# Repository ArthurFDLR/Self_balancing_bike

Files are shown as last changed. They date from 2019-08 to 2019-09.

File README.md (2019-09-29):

# Self_balancing_bike

The final objective is to stabilize a bike using a flywheel. For now, I'm focusing on the stabilisation part : reading IMU data, precise DC motor control, PID controller ...

## Mecanical parts
### Frame 
I wanted something as simple as possible. I initialy printed a single arm supported wheel. However the mass of the wheel was way to much for the frame to handle. I added a second arm to hold the wheel thanks to a bearing. The height of the rotationnal axis is variable. Once in place, toothpicks lock the position.

### Flywheel
Theorically I could determine the momentum of the wheel. However the equation depends on way to many factors to be really usable from the ground up. I've simply use an aluminum wheel I had laying around. I'll eventually change it to achieve a better efficiency.

## Electronics

Nothing to fancy here. A simple Nano v3 to compute the data, a MD13S motor driver with a Pololu 6V 25mm motor and an MPU6050. I'll certainly swap those componnent for a single board like a Storm32-BGC V1.32 usually used for gimbals. It has all I need (and even more) for this project.

## Code

The main goal is to get an efficiente code that can run as fast as possible on the Nano. For exemple I access directly to Atmega's registers during ISR. Currently runing at ~60Hz.
To ease tunings, a serial communication between the board and the IDE is setup to tune certain values and choose mode in real-time. 

| Char command | Mode |
| - | --- |
| 1 | Running stabilisation |
| 2 | Motor test w/ potentiometer |
| 3 | Setpoint variation viewer |
| 4 | IMU data viewer |
| p | KP tuning |
| i | KI tuning |
| d | KD tuning |
| s | KS tuning |

I use the incredible [library i2cdevlib from jrowberg](https://github.com/jrowberg/i2cdevlib) which takes advantage of the internal DMP of the board to read the IMU.

```c++
// IN   // NULL
// OUT  // ypr : float[3]
// DO   // Read last available data from MPU6050. Update {Yaw,Pitch,Roll} angular position in ypr
void Update_leanAngle();

// IN   // ypr                           : float[3]
        // IMU_time_now, IMU_time_prev   : uint32_t
// OUT  // leanAngle                     : float
        // leanAngle_smoothed            : float
        // leanAngleError                : float
        // leanAngle_Integer             : float
        // leanAngle_derivative          : float
        // leanAngle_derivative_smoothed : float
        // leanAngleSetPoint             : float
// TUNE // leanAngle_Filter              : float
        // leanAngle_Derivative_Filter   : float
        // leanAngle_HeavyFilter         : float
        // setPoint_KP, setPoint_KD      : uint32_t
// DO   // Calculates lean angle and its derivative and integral from ypr.
        // Filter results to eliminate noise (exponential filter)
void leanAngle_compute();

// IN   // motorCommandPwm : int16_t
        // motorSpeedRpm   : uint32_t
// OUT  // NULL
// TUNE // motorCommandPwm_Offset         : int16_t
        // motorCommandPwm_Starter_Offset : int16_t
        // motorLimitPwm                  : int16_t
// DO   // Filters command and send to motor. Smooth start, offset, limit ...
void Set_Motor_Speed();

// IN   // motorTickCount    : int32_t
// OUT  // motorSpeedRpm     : uint32_t
        // motorDirection    : int8_t
        // motorAccelerating : bool
// TUNE // motorFilter : float
// DO   // Interpret encoder ticks to give motor speed
void Update_MotorData();

// IN   // leanAngleError       : float
        // leanAngle_Integer    : float
        // leanAngle_derivative : float
        // motorDirection       : int8_t
        // motorSpeedRpm        : uint32_t
// OUT  // PID_output           : double
// TUNE // KP, KI, KD, KS       : float
        // motorFriction        : uint32_t
        // motorLimitPwm        : int16_t
// DO   // Compute data to give command w/PID controller
void Update_MotorData();
```

## Current state

IMU data viewer (http://www.youtube.com/watch?v=QBGMhSDM0Ms "IMU data viewer")

I didn't find any way to start the motor without it giving a strong hit. It leads to an overshooting when trying to stabilize when the motor is still, for any KP ... I tried to set the standard rotation speed around PWM=40. I achieved some good reaction but only one falling side at a time. The braking power of the motor is way stronger than it's acceleration. It would recquiere an adaptive PID tuning given wheel rotation acceleration sign. Even then, it would be higly unefficient.
I'm now trying to fit a gimbal brushless motor - 120kv -. With a descent control method, I'll eventually overcome the jerkyness at low speed.

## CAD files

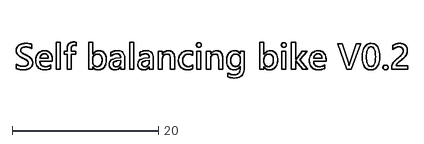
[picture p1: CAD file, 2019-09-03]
3D_Models/Catia_project/txt_mark.dxf
53.5 x 4.93

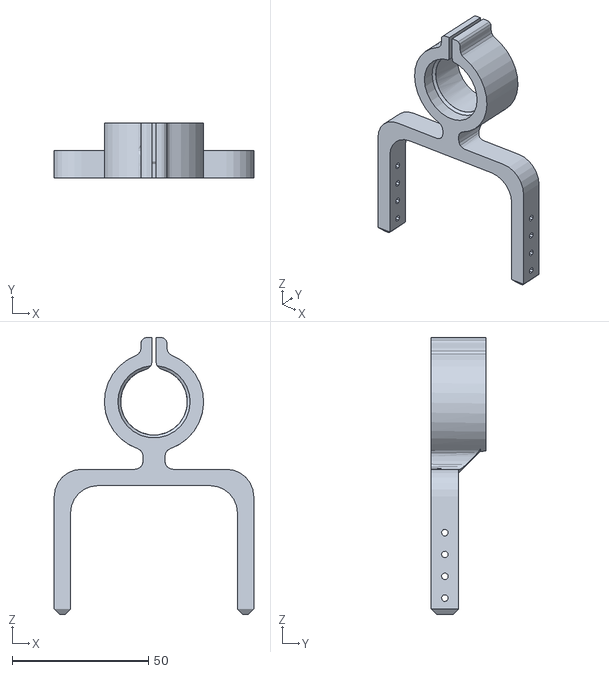
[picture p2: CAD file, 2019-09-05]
3D_Models/Motor_holder.stl
73.2 x 20.0 x 101.6

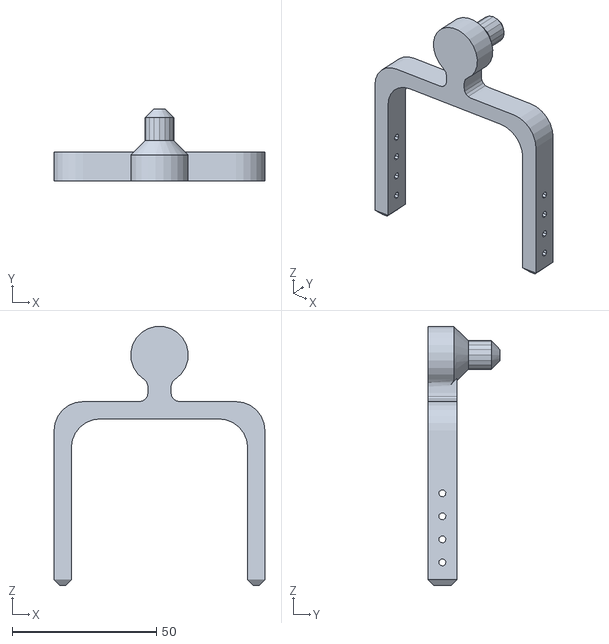
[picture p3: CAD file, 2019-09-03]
3D_Models/Wheel_holder.stl
73.2 x 25.0 x 89.9

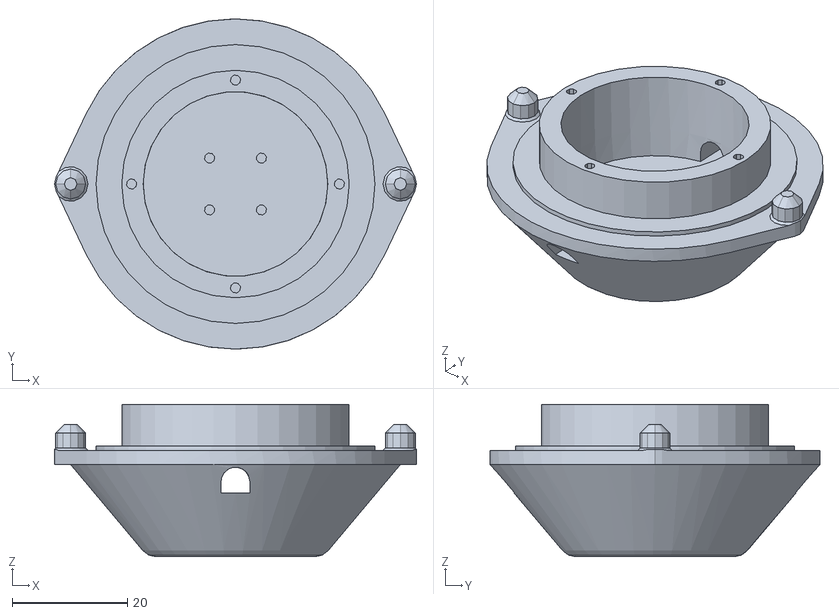
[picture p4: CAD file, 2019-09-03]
3D_Models/InertiaWheel_mount_front_V3.stl
62.7 x 57.2 x 26.4

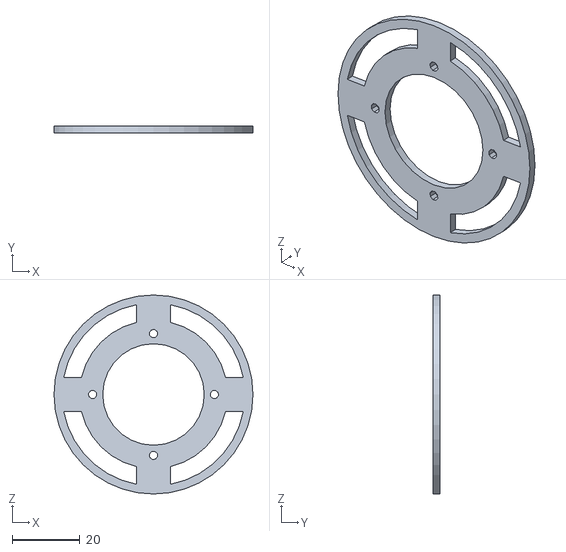
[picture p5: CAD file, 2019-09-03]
3D_Models/InertiaWheel_mount_back.stl
58.8 x 2.00 x 58.8

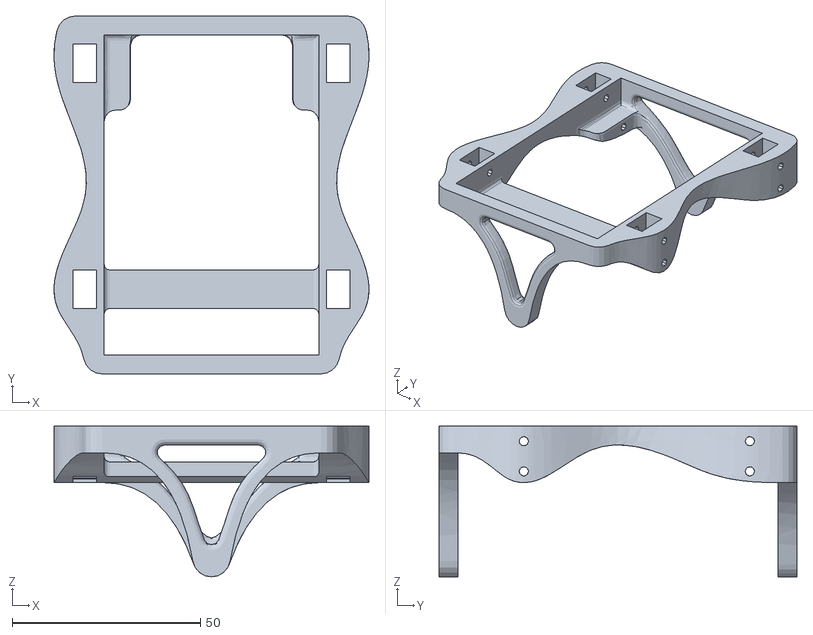
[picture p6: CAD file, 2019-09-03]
3D_Models/Lower_part_balancing.stl
83.6 x 95.0 x 40.0

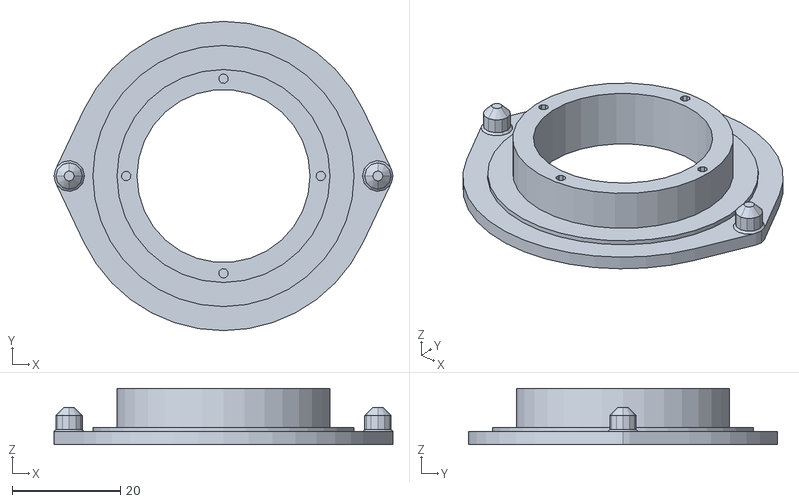
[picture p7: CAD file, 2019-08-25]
3D_Models/InertiaWheel_mount_V1.stl
62.7 x 57.2 x 10.4

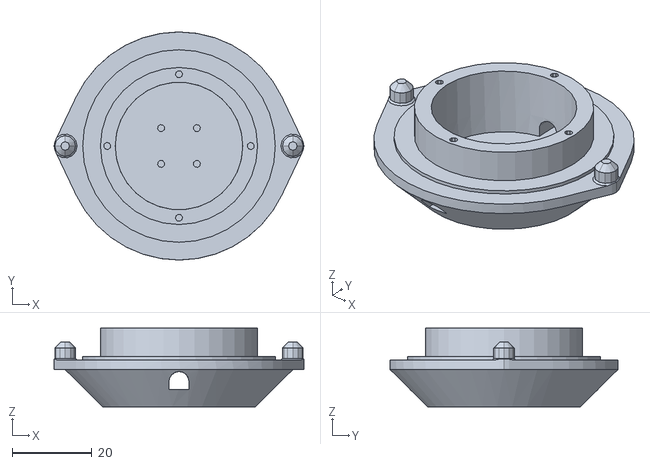
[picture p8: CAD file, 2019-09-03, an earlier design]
3D_Models/InertiaWheel_mount_front_V2.stl
62.7 x 57.2 x 19.8

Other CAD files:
3D_Models/Catia_project/InertiaWheel_mount_back.CATPart
3D_Models/Catia_project/InertiaWheel_mount_front.CATPart
3D_Models/Catia_project/Lower_part_balancing.CATPart
3D_Models/Catia_project/Motor_holder.CATPart
3D_Models/Catia_project/Pololu_DC_Motor.CATPart
3D_Models/Catia_project/Product1.CATProduct
3D_Models/Catia_project/Skeleton_stabilized_bike.CATPart
3D_Models/Catia_project/Wheel_holder.CATPart
3D_Models/Catia_project/test.CATPart
3D_Models/Catia_project/test_bearing.CATPart
3D_Models/Catia_project/testing_frame.CATPart

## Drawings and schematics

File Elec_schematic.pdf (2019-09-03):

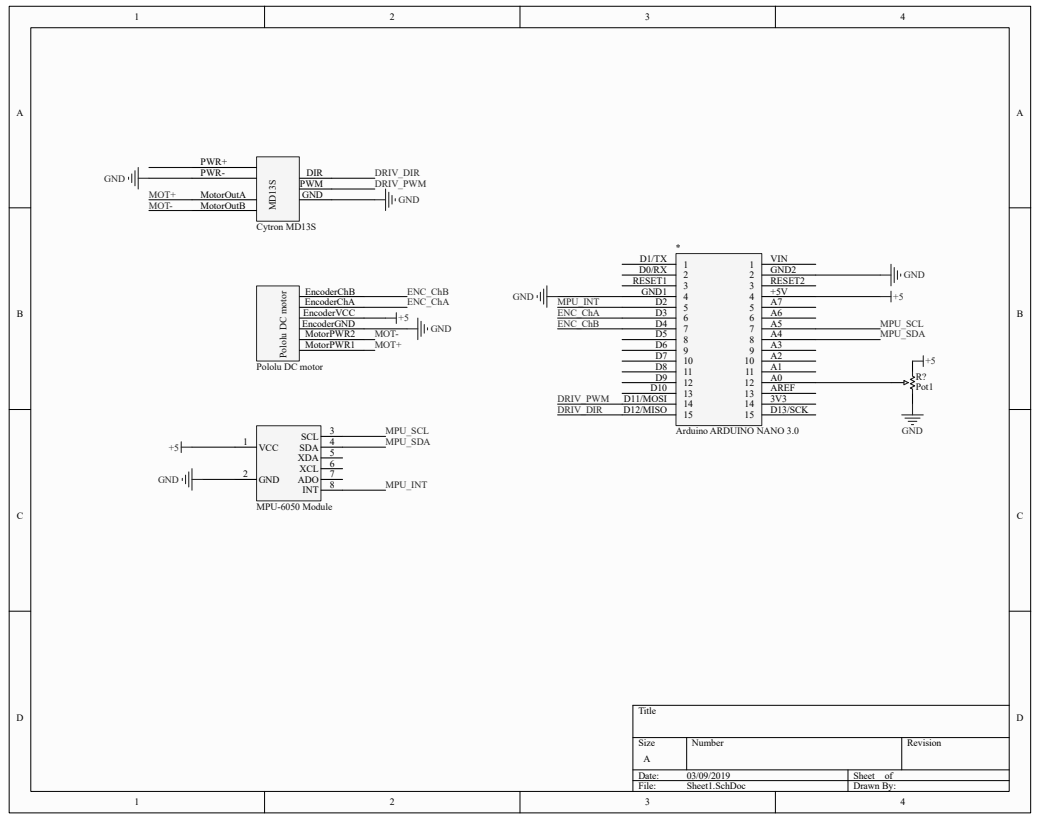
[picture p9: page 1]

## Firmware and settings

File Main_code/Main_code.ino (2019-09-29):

/**   SELF STABILIZED BIKE

   note : - Run on arduino nano
          - Controle and measure DC motor's speed
          - Read IMU data
          - Compute PIDs data

   author : Arthur FINDELAIR, github.com/ArthurFDLR
   date : September 2019
*/

// =============================
// ===       Libraries       ===
// =============================

#include <I2Cdev.h>
#include <MPU6050_6Axis_MotionApps20.h>
#include <Wire.h>

// ================================================
// ===       VARIABLES and INSTANTIATIONS       ===
// ================================================

/*--------------*/
/*   GLOBAL     */
/*--------------*/

char machineState = '0';
char serialViewerMode = '0';
uint16_t timePrev = 0;
uint16_t computationTime = 0;
const int8_t workingFrequency = 65; //Hz

/*----------------------*/
/*   PID controller     */
/*----------------------*/

// Tunings
uint32_t KP = 50;
uint32_t KI = 0;
uint32_t KD = 0;
uint32_t KS = 0;

uint32_t motorFriction = 0;

uint32_t setPoint_KP = 0; //100
uint32_t setPoint_KD = 0;  //45

// Exponential filter parameters
const float leanAngle_Filter = 0.9;
const float leanAngle_HeavyFilter = 0.4;
const float setPoint_filter = 0.8;
const float leanAngle_Derivative_Filter = 0.6;

// Variables
float leanAngle; //degrees
float leanAngle_raw;
float leanAngle_prev;
float leanAngle_smoothed;
float leanAngle_smoothed_prev;
float leanAngleError = 0;

float leanAngleSetPoint = 2.7;
float leanAngleSetPoint_prev = 0;
float leanAngleSetPoint_raw = 0;

float leanAngle_derivative;
float leanAngle_derivative_prev;
float leanAngle_derivative_smoothed;
float leanAngle_derivative_smoothed_prev;

float leanAngle_Integer;

double P_control, I_control, D_control, S_control;
double PID_output = 0;

float PID_friction;

/*---------------*/
/*   ENCODER     */
/*---------------*/

const float motorFilter = 0.5;       // [0,1] exponential filter parameter
const float encoderCountRev = 212.0;
const int8_t pinEncoderAInterrupt = 3; //PD3
const int8_t pinEncoderB = 4;  //PD4
const char registerMaskPIND = 0b00011000; //Show pin

volatile int32_t motorTickCount = 0;
uint32_t motorTimePrev = 0; //Some of those variables can be ignored/simplify ; Microsec
uint32_t motorTimeNow = 0;
uint32_t motorTimeDiff = 0;

uint32_t motorSpeedRpm = 0;
uint32_t motorSpeedRpmRaw = 0;
uint32_t motorSpeedRpmPrev = 0;
int8_t motorDirection = 0; // {-1;0;1} with 0 => stopped
bool motorAccelerating = false;

/*-----------*/
/*   IMU     */
/*-----------*/

const uint8_t pinIMUInterrupt = 2;
MPU6050 mpu;

// MPU control/status vars
bool dmpReady = false;  // set true if DMP init was successful
uint8_t mpuIntStatus;   // holds actual interrupt status byte from MPU
uint8_t devStatus;      // return status after each device operation (0 = success, !0 = error)
uint32_t packetSize;    // expected DMP packet size (default is 42 bytes)
uint32_t fifoCount;     // count of all bytes currently in FIFO
uint8_t fifoBuffer[64]; // FIFO storage buffer

// orientation/motion vars
Quaternion q;           // [w, x, y, z]         quaternion container
VectorFloat gravity;    // [x, y, z]            gravity vector

float ypr[3]; // [yaw, pitch, roll]
uint32_t IMU_time_prev, IMU_time_now; // to compute leanAngle derivative and integer

/*----------------*/
/*   DC MOTOR     */
/*----------------*/

const int8_t pinPotentiometer = 0; // A0
const int8_t pinEscPWM = 11;
const int8_t pinEscDir = 12;
const int16_t motorLimitPwm = 128; //Stay under 6V for 12V alim.
const int16_t motor_Starter_SpeedLimit = 70;
// DC_motor motor( pinEscPWM, pinEscDir, motorLimitPwm);  // PWM = Pin 11, DIR = Pin 12.
int16_t motorCommandPwm = 0;
int16_t motorCommandPwm_prev = 0;
int16_t motorCommandPwm_Offset = 25;
int16_t motorCommandPwm_Starter_Offset = 120;

// =====================================
// ===       ARDUINO PROCESSES       ===
// =====================================

void setup() {
  Wire.begin(); // join I2C bus (I2Cdev library doesn't do this automatically)
  Serial.begin(115200);
  Serial.setTimeout(5);

  Encoder_Setup();
  IMU_setup();

  Serial.println(F("\n\nReady to run !"));
  Serial.print(F("Mode set to ")); Serial.println(machineState);
  timePrev = millis();
}

void loop() {
  if (millis() - timePrev > 1000 / workingFrequency) {

    if (Serial.available()) {
      analogWrite(pinEscPWM, 0); //Shut down motor
      machineState = Serial.read();
      serialViewerMode = machineState;
      Serial.print(F("\n\nState set to ")); Serial.println(machineState);

      if (machineState == '1' | machineState == '3' | machineState == '4') { // reset computing
        mpu.resetFIFO();
        IMU_time_prev = micros();
        IMU_time_now = micros();
        PID_output = 40;
      }
    }

    timePrev = millis();

    switch (machineState) {

      case '1' : // PID controlled mode
        Update_MotorData(); // Update value of motorSpeedRpm (filtered) and motorDirection; both used to compute PIDs
        Update_leanAngle(); // Update the value of ypr[]; ypr[1] is used to compute leanAngle
        leanAngle_compute();
        PID_compute();
        Set_Motor_Speed();
        break;

      case '2' : // Motor test
        Update_MotorData(); // Update value of motorSpeedRpm (filtered) and motorDirection; both used to compute PIDs
        motorCommandPwm = - map(analogRead(A0), 0, 1023, 0, motorLimitPwm);
        Set_Motor_Speed();
        break;

      case '3' : // Setpoint tuning
        Update_MotorData();
        Update_leanAngle(); // Update the value of ypr[]; ypr[1] is used to compute leanAngle
        leanAngle_compute();
        PID_compute();
        break;

      case '4' : // IMU Viewer
      Update_MotorData();
        Update_leanAngle(); // Update the value of ypr[]; ypr[1] is used to compute leanAngle
        leanAngle_compute();
        //PID_compute();
        break;

      case 'p' : // Update KP
        KP = Update_uint32_serial(KP);
        break;

      case 'i' : // Update KI
        KI = Update_uint32_serial(KI);
        break;

      case 'd' : // Update KD
        KD = Update_uint32_serial(KD);
        break;

      case 's' : // Update KS
        KS = Update_uint32_serial(KS);
        break;

      default:
        break;
    }

    computationTime = millis() - timePrev;
    Serial_viewer(serialViewerMode);
  }
  else {
    //Serial.println("_"); //Check working frequency calibration
  }
}

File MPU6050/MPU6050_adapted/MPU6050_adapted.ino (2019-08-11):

// https://www.i2cdevlib.com/docs/html/class_m_p_u6050.html


#include "I2Cdev.h"
#include "MPU6050_6Axis_MotionApps20.h"
#include "Wire.h"

MPU6050 mpu;

const int pinIMUInterrupt = 2;  // use pin 2 on Arduino Uno & most boards

// MPU control/status vars
bool dmpReady = false;  // set true if DMP init was successful
uint8_t mpuIntStatus;   // holds actual interrupt status byte from MPU
uint8_t devStatus;      // return status after each device operation (0 = success, !0 = error)
uint16_t packetSize;    // expected DMP packet size (default is 42 bytes)
uint16_t fifoCount;     // count of all bytes currently in FIFO
uint8_t fifoBuffer[64]; // FIFO storage buffer

// orientation/motion vars
Quaternion q;           // [w, x, y, z]         quaternion container
VectorFloat gravity;    // [x, y, z]            gravity vector
float ypr[3];           // [yaw, pitch, roll]   yaw/pitch/roll container and gravity vector


// ================================================================
// ===               INTERRUPT DETECTION ROUTINE                ===
// ================================================================

volatile bool mpuInterrupt = false;     // indicates whether MPU interrupt pin has gone high
void ISR_dmpDataReady() {
  mpuInterrupt = true;
}

// ================================================================
// ===                      FUNCTION IMU                        ===
// ================================================================

void setup_IMU() {
  // initialize device
  Serial.println(F("Initializing I2C devices..."));
  mpu.initialize();
  pinMode(pinIMUInterrupt, INPUT);

  // verify connection
  Serial.println(F("Testing device connections..."));
  Serial.println(mpu.testConnection() ? F("MPU6050 connection successful") : F("MPU6050 connection failed"));

/*
  // wait for ready
  Serial.println(F("\nSend any character to begin DMP programming and demo: "));
  while (Serial.available() && Serial.read()); // empty buffer
  while (!Serial.available());                 // wait for data
  while (Serial.available() && Serial.read()); // empty buffer again
*/
  // load and configure the DMP
  Serial.println(F("Initializing DMP..."));
  devStatus = mpu.dmpInitialize();

  // Useless since auto-calibration
  // supply your own gyro offsets here, scaled for min sensitivity
  mpu.setXGyroOffset(220);
  mpu.setYGyroOffset(76);
  mpu.setZGyroOffset(-85);
  mpu.setZAccelOffset(1788); // 1688 factory default for my test chip

  // make sure it worked (returns 0 if so)
  if (devStatus == 0) {
    // Calibration Time: generate offsets and calibrate our MPU6050
    mpu.CalibrateAccel(6);
    mpu.CalibrateGyro(6);
    mpu.PrintActiveOffsets();
    // turn on the DMP, now that it's ready
    Serial.println(F("Enabling DMP..."));
    mpu.setDMPEnabled(true);

    // enable Arduino interrupt detection
    Serial.print(F("Enabling interrupt detection (Arduino external interrupt "));
    Serial.print(digitalPinToInterrupt(pinIMUInterrupt));
    Serial.println(F(")..."));
    attachInterrupt(digitalPinToInterrupt(pinIMUInterrupt), ISR_dmpDataReady, RISING);
    mpuIntStatus = mpu.getIntStatus();

    // set our DMP Ready flag so the main loop() function knows it's okay to use it
    //Serial.println(F("DMP ready! Waiting for first interrupt..."));
    dmpReady = true;

    // get expected DMP packet size for later comparison
    packetSize = mpu.dmpGetFIFOPacketSize();
  } else {
    // ERROR!
    // 1 = initial memory load failed
    // 2 = DMP configuration updates failed
    // (if it's going to break, usually the code will be 1)
    Serial.print(F("DMP Initialization failed (code "));
    Serial.print(devStatus);
    Serial.println(F(")"));
  }
}

void Update_YPR() {
  if (!dmpReady) {
    Serial.println("Shit failed yo");
    return;                                               // if programming failed, don't try to do anything
  }

  // wait for MPU interrupt or extra packet(s) available
  while (!mpuInterrupt && fifoCount < packetSize) {
    if (mpuInterrupt && fifoCount < packetSize) {
      // try to get out of the infinite loop
      fifoCount = mpu.getFIFOCount();
    }
    // other program behavior stuff here
    // if you are really paranoid you can frequently test in between other
    // stuff to see if mpuInterrupt is true, and if so, "break;" from the
    // while() loop to immediately process the MPU data
  }


  mpuInterrupt = false;                 // reset interrupt flag
  mpuIntStatus = mpu.getIntStatus();    //get INT_STATUS byte
  fifoCount = mpu.getFIFOCount();       // get current FIFO count

  if ((mpuIntStatus & _BV(MPU6050_INTERRUPT_FIFO_OFLOW_BIT)) || fifoCount >= 1024) {  // check for overflow (this should never happen unless our code is too inefficient)
    mpu.resetFIFO();        // reset so we can continue cleanly
    Serial.println(F("FIFO overflow!"));
  }

  else if (mpuIntStatus & _BV(MPU6050_INTERRUPT_DMP_INT_BIT)) {     // otherwise, check for DMP data ready interrupt (this should happen frequently)

    while (fifoCount < packetSize) {   // wait for correct available data length, should be a VERY short wait
      delay(1);
      fifoCount = mpu.getFIFOCount();
      mpuIntStatus = mpu.getIntStatus();
    }

    while (fifoCount >= packetSize) { // Lets catch up to NOW, someone is using the dreaded delay()!
      mpu.getFIFOBytes(fifoBuffer, packetSize);
      // track FIFO count here in case there is > 1 packet available
      // (this lets us immediately read more without waiting for an interrupt)
      fifoCount -= packetSize;
    }

    mpu.dmpGetQuaternion(&q, fifoBuffer);
    mpu.dmpGetGravity(&gravity, &q);
    mpu.dmpGetYawPitchRoll(ypr, &q, &gravity);
  }
}

// ================================================================
// ===                      INITIAL SETUP                       ===
// ================================================================

void setup() {

  Wire.begin(); // join I2C bus (I2Cdev library doesn't do this automatically)
  Wire.setClock(400000); // 400kHz I2C clock. By default : 100kHz
  Serial.begin(115200);

  setup_IMU();
}

// ================================================================
// ===                    MAIN PROGRAM LOOP                     ===
// ================================================================

void loop() {
  
  Update_YPR();


  // display Euler angles in degrees
  Serial.print("ypr (zyx)\t");
  Serial.print(ypr[0] * 180 / M_PI);
  Serial.print("\t");
  Serial.print(ypr[1] * 180 / M_PI);
  Serial.print("\t");
  Serial.println(ypr[2] * 180 / M_PI);

  
}

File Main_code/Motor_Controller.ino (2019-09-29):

/**   SELF STABILIZED BIKE - MOTOR

   note : This part of the code used to be a library,
          it eventually is easier to read and debug without encapsulation

   author : Arthur FINDELAIR, github.com/ArthurFDLR
   date : September 2019
*/

void Motor_Setup() {
  pinMode(pinEscPWM, OUTPUT);
  pinMode(pinEscDir, OUTPUT);
  digitalWrite(pinEscPWM, LOW);
  digitalWrite(pinEscDir, LOW);
}

void Set_Motor_Speed() {

  motorCommandPwm = (int)(PID_output);

  // Motor launching
  if ( (abs(motorSpeedRpm) < 30) & (abs(motorCommandPwm) < motorCommandPwm_Offset)) { // & (abs(motorCommandPwm) > 0)
    motorCommandPwm += ((motorCommandPwm > 0) ? 1 : - 1) * motorCommandPwm_Starter_Offset ;
  } else if (abs(motorCommandPwm) > 1 ) {
    motorCommandPwm += ((motorCommandPwm > 0) ? 1 : - 1) * motorCommandPwm_Offset;
  }


  /*
    if (abs(motorCommandPwm) > motorCommandPwm_Offset){
    motorCommandPwm += ((motorCommandPwm > 0) ? 1 : - 1) * motorCommandPwm_Offset;
    }   else if ((abs(motorCommandPwm) > 1) & (abs(motorCommandPwm) < motorCommandPwm_Offset)){
    motorCommandPwm += ((motorCommandPwm > 0) ? 1 : - 1) * ( motorCommandPwm_Offset/2 + motorCommandPwm );
    }

    else if (abs(motorCommandPwm) > 10) {
    motorCommandPwm *= 2 ;
    } else if (abs(motorCommandPwm) > 1){
    motorCommandPwm = 10;
    }
  */

  // Limit motor command
  if (motorCommandPwm > motorLimitPwm) {
    motorCommandPwm = motorLimitPwm;
  } else if (motorCommandPwm < -motorLimitPwm) {
    motorCommandPwm = -motorLimitPwm;
  }

  // Write speed
  if ((abs(motorCommandPwm - motorCommandPwm_prev) > motorCommandPwm_Offset - 20) & (abs(motorSpeedRpm) < 200)) {
    motorCommandPwm = motorCommandPwm * 0.4 + motorCommandPwm_prev * (1.0 - 0.4);
    motorCommandPwm_prev = motorCommandPwm;
  }

  if (motorCommandPwm >= 0) {
    analogWrite(pinEscPWM, motorCommandPwm);
    digitalWrite(pinEscDir, LOW);
  } else {
    analogWrite(pinEscPWM, -motorCommandPwm);
    digitalWrite(pinEscDir, HIGH);
  }

}

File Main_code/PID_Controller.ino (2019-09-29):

/**   SELF STABILIZED BIKE - PID
 *    
 * note : Might need anti wind-up, derivative filtering and automatic setpoint adjustment
 *
 * author : Arthur FINDELAIR, github.com/ArthurFDLR
 * date : September 2019
 */

// ==============================================
// ===             FUNCTION PID               ===
// ==============================================

void leanAngle_compute(){ // Seems to work --> serialViewerMode=1
  
  leanAngle_prev = leanAngle;
  leanAngle_raw = ypr[1] * 180 / M_PI; // To cut down noises : round((ypr[1] * 180 / M_PI) * angle_Rounding_Value) / angle_Rounding_Value;
  leanAngle = leanAngle_raw * leanAngle_Filter + leanAngle_prev * (1.0 - leanAngle_Filter);
  
  leanAngleError = leanAngleSetPoint - leanAngle;

  leanAngle_Integer += leanAngleError * (IMU_time_now - IMU_time_prev) / 1000000.0; // Might need anti wind-up

  leanAngle_derivative_prev = leanAngle_derivative;
  leanAngle_derivative = (float) ((leanAngle - leanAngle_prev) / ((IMU_time_now - IMU_time_prev) / 1000000.0)) * leanAngle_Derivative_Filter + leanAngle_derivative_prev * (1.0 - leanAngle_Derivative_Filter);

  // Automatic setup adjustment
  leanAngle_smoothed_prev = leanAngle_smoothed;
  leanAngle_smoothed = leanAngle * leanAngle_HeavyFilter + leanAngle_smoothed_prev * (1.0 - leanAngle_HeavyFilter);
  leanAngle_derivative_smoothed_prev = leanAngle_derivative_smoothed;
  leanAngle_derivative_smoothed = leanAngle_derivative * leanAngle_HeavyFilter + leanAngle_derivative_smoothed_prev * (1.0 - leanAngle_HeavyFilter);

  leanAngleSetPoint_prev = leanAngleSetPoint;
  //leanAngleSetPoint -= (float) (setPoint_KP * leanAngleError - leanAngle_derivative_smoothed * setPoint_KD) / 10000.0;
  //leanAngleSetPoint = leanAngleSetPoint_raw * setPoint_filter + leanAngleSetPoint * (1.0 - setPoint_filter);
}


void PID_compute(){
  
  P_control = KP * leanAngleError;
  I_control = KI * leanAngle_Integer;
  D_control = KD * leanAngle_derivative;

  PID_friction = motorDirection * motorFriction;

  S_control = KS * motorDirection * (motorSpeedRpm / 60.0);

  PID_output += (P_control + I_control + D_control + PID_friction + S_control) / 100;

  if (PID_output > motorLimitPwm) {
    PID_output = motorLimitPwm;
  } else if (PID_output < -motorLimitPwm) {
    PID_output = -motorLimitPwm;
  }

  
  
  //motorCommandPwm = (int)(PID_output + PID_friction + S_control);
  //motorCommandPwm = ((motorCommandPwm > motorLimitPwm) ? motorLimitPwm : motorCommandPwm);
  //motorCommandPwm = ((motorCommandPwm < -motorLimitPwm) ? -motorLimitPwm : motorCommandPwm);
  //motorCommandPwm = round(constrain( (int)(PID_output + PID_friction + S_control) ,-motorLimitPwm ,motorLimitPwm));

}

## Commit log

2019-08-11 Self-written code to read encoder
    The libraries I found are not as precise as what I can achieve myself with this configuration. Minor changes are made on filtering
2019-08-25 Add 3D models
    [InertiaWheel_mount.CATPart, InertiaWheel_mount.stl, Lower_part_balancing.CATPart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]
2019-09-03 Update 3D models
    [InertiaWheel_mount.CATPart, InertiaWheel_mount.stl, InertiaWheel_mount_V1.stl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]
2019-09-03 Update 3D models + ADD schematic
    [InertiaWheel_mount_front.CATPart, Motor_holder.CATPart, Motor_holder.stl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]
2019-09-05 Encoder library
    ISR can't be simply called in a class ...
    https://www.onetransistor.eu/2019/05/arduino-class-interrupts-and-callbacks.html
    [Motor_holder.CATPart, Motor_holder.stl]
2019-09-05 Separate encoder part and global + 3D files
2019-09-06 Major update
    Fuse IMU and Motor controller codes. Screen computation time.
2019-09-12 Add PID
2019-09-12 IMU calibration + PIDS
2019-09-13 Fix motor speed reading
    float to int conversion
    [Encoder_manager.ino, Main_code.ino]
2019-09-14 First PID test
2019-09-14 Major update of motor command
    starter + replace library
    [Main_code.ino, Motor_Controller.ino, PID_Controller.ino]
2019-09-17 PID tuning
    Need to smooth out motor control ...
